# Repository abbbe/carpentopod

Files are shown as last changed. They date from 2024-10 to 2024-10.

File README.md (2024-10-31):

# Table of Contents

- [Credits](#credits)
- [Community](#community)
- [Downloadable Content](#downloadable-content)
- [Intro](#intro)
- [Design](#design)
  - Linkage
  - Legs
  - Leg Pair + Frame and Crank
  - Frame and Crank
  - Gearbox and Frame
  - Crank
  - Six Legs
  - Full Assembly
  - Editable Design Files
- [Printing](#printing)
- [Assembly](#assembly)
- [Electronics](#electronics)
- [Firmware](#firmware)

**Update 2024-10-31**

* The square shafts were originally printed in PLA-CF, but two out of 3 got damaged very quickly. I reassembled the whole thing using 8x8mm steel rods. Here in Belgium these rods can be bought in DIY stores. You'll have to cut them to size, see dimensions in the build log below.
* Manually chamfered the round parts of the cranks, to make it less likely to collide with the bottop part of the legs.
* Added a M8 nut which hides under the outter black spacers, to make the frame more rigid.
* Added rounded shoes (printed in PETG), to let feet slide sideways during turns.

All these changes (except chamfer of the cranks) is in the latest version of STEP models.

# Credits

This project was inspired by [Carpentopod](https://www.decarpentier.nl/carpentopod) created by Giliam de Carpentier, all credits should go to him.

# Useful Content

Here is a Youtube clip of the [thing walking steered using Nintendo controller](https://youtu.be/jmLX-odWrtY):
IMAGE ALT TEXT HERE (https://www.youtube.com/watch?v=jmLX-odWrtY)

The latest Fusion 360 models in STEP format is uploaded into the [STP/](https://github.com/abbbe/carpentopod-v43/tree/main/STP) folder on GitHub. Normally the STEP file includes all the subcomponents. (If you want individual models of the elements described in "Design" section, check previous commits). Once you open the model you should get something like this:
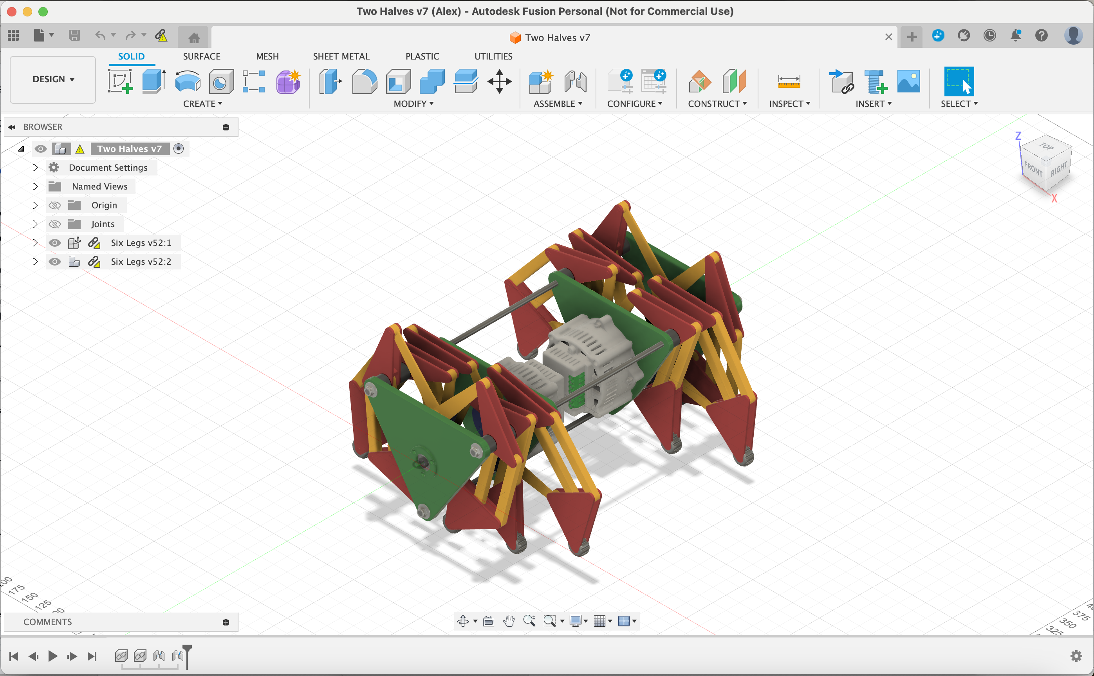
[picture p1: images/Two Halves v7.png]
Two Halves v7 - Thumbnail


An interactive 3D model is available on the [Autodesk site](https://a360.co/3A7hhCD).

Here is a screen recording of the [animation of the joint movements in Fusion 360](https://youtu.be/IclcQic5kn8) on YouTube. Done from different view angles, with some legs and plates removed to make the crankshaft movements visible. I did not recreate it since the original upload, so there are no shoes (you can see those via the Autodesk link above).

Printable 3MF files are uploaded into the [3MF/](https://github.com/abbbe/carpentopod-v43/tree/main/3MF) folder. Made in OrcaSlicer, printed on a Bambu X1C with 0.4mm hardened steel nozzle (see the Printing section below for more details).

The models are also published on [Printables](https://www.printables.com/model/1052837-carpentopod-v43).

I have created a [thread](https://discord.com/channels/1299814326185627702/1300201396834140271) on Giliam's Discord server, if you have any questions feel free to ask there. Or create GitHub issue or a pull request.

# Intro

I have been playing with Fusion 360 and various linkages for couple months when I saw a video of the [Carpentopod](https://www.decarpentier.nl/carpentopod) published by Giliam De Carpenter. He was kind enough to release exact linkage dimensions. I figured it could be a nice Fusion 350 challenge to design the mechanism behind the scene.

As you will see below, I have focused mostly on the mechanical side, not the artistic value of the piece. There is rudimentary electronics curcuitry and firmware to control it, I have described it on the high level at the end of the document.

At this point as I have no particular plans to continue with this project. If you found this design entertaining or useful, I will be happy to hear about it. Feel free to contact me if you have any questions.

And as far as any intellectual property (accidentally) created by me goes -- I am licensing it away under two conditions: (1) you put a star to this Github repo and (2) you will not use it for any military purposes. **Make robots, not war!**

# Design

## Linkage

I have turned the original linkage diagram black and white for easier printing and named each joint.
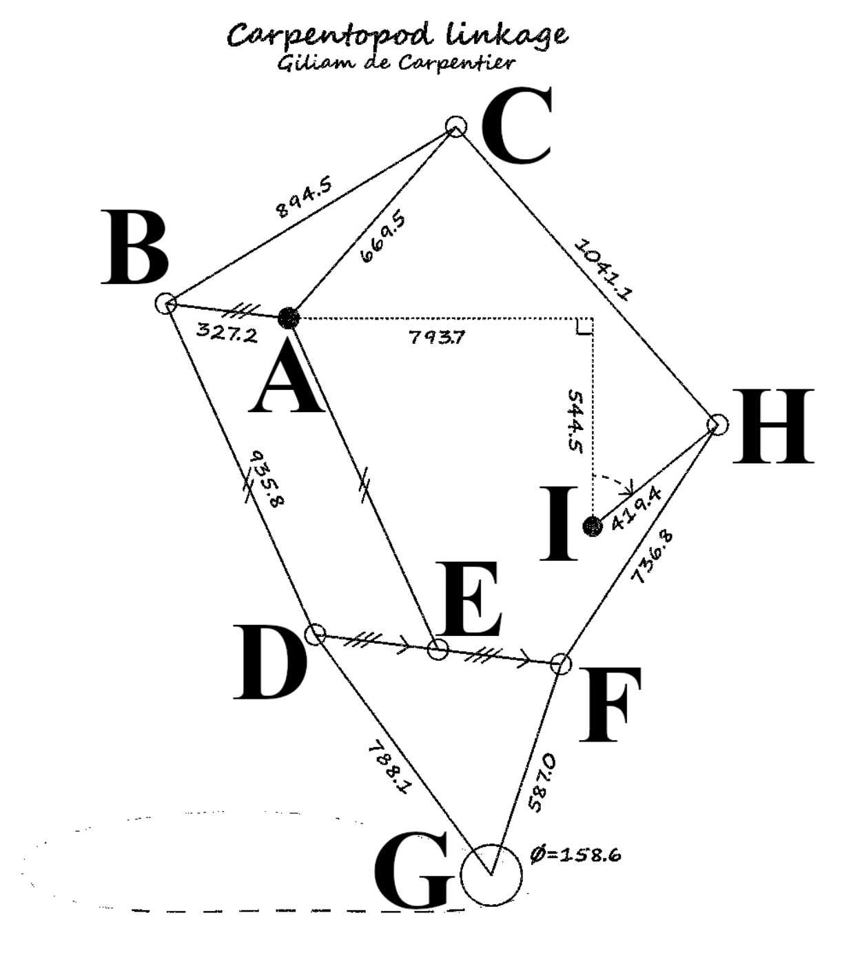
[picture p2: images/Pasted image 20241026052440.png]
Linkage Diagram


## Legs

The first part I designed was a leg. I have made an attempt to parameterise the design. It was not obvious what units Giliam's diagram used exactly, so I have included a scaling factor which I can tune the size of the model for my printer.
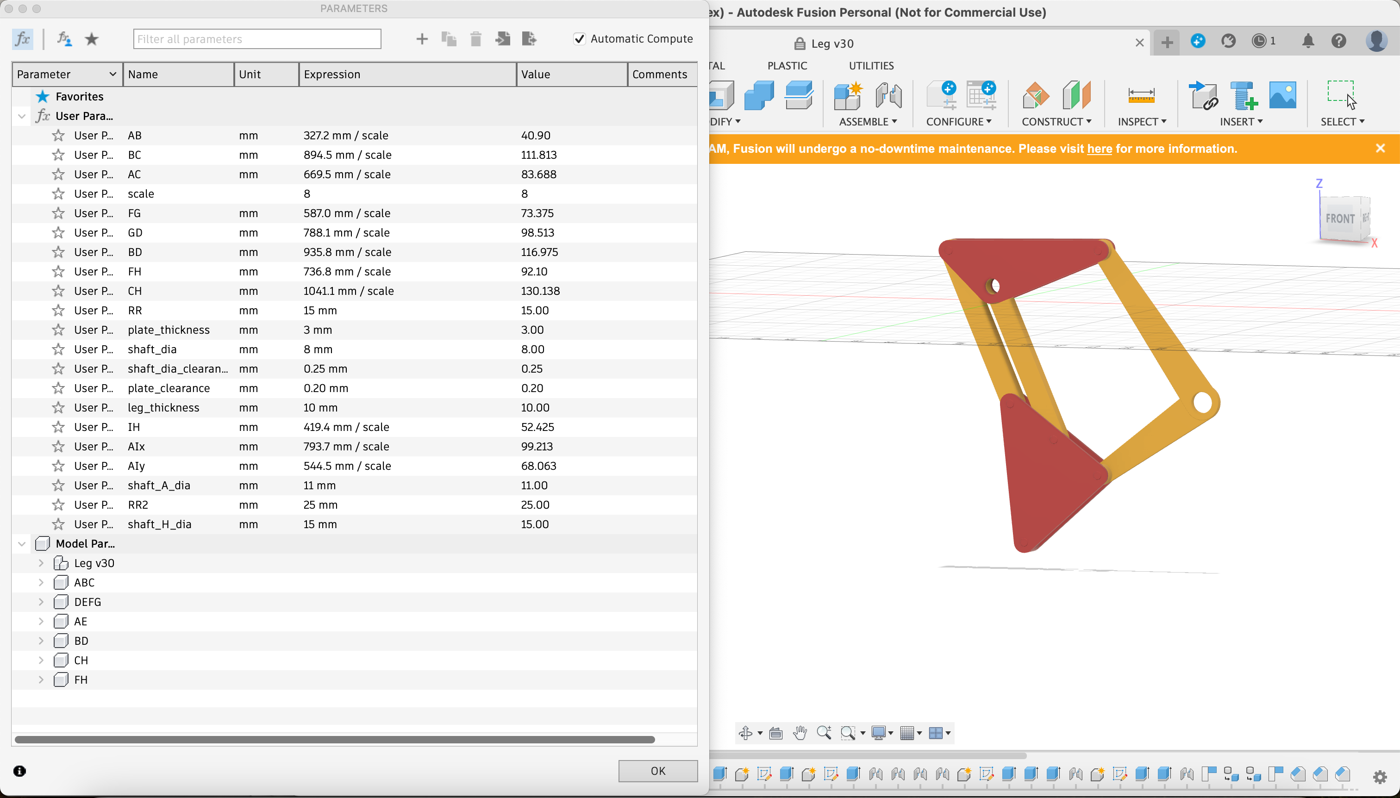
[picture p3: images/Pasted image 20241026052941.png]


Unfortunately, I couldn't find a way to share parameters between designs in Fusion 360. So some of these values ended up being copy-pasted into other designs. If you know how to do this properly, please tell me.

The design is as simplistic as it gets, I have made no attempt to replicate the beautiful curves of Carpentopod's legs. Here is another view without the top plates:
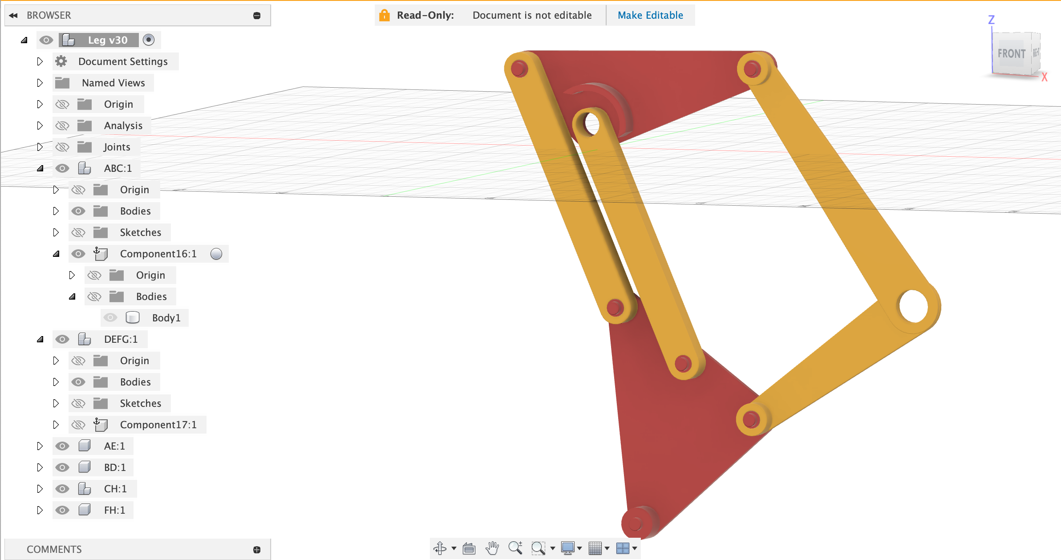
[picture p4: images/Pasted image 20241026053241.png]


To keep things 3D-printable I had to make a separate spacer:
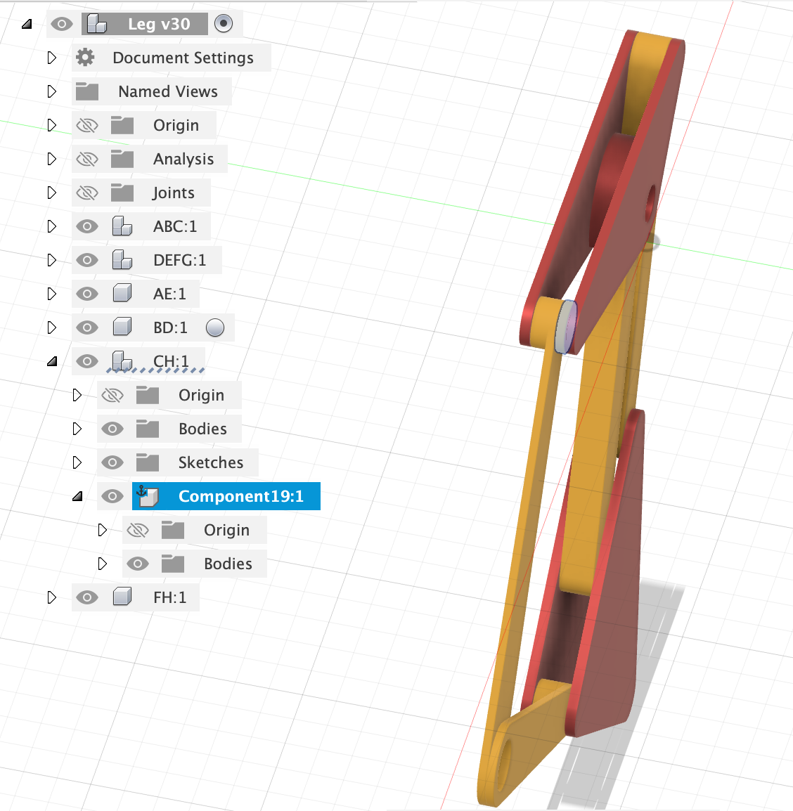
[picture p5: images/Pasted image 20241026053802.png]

I have randomly chosen the thickness of the larger levers (AE, BD) to be 10mm. It means levers CH and FH became 2.5mm thick (there was no spacing in between the levers, but there is spacing between the yellow levers and the red plates). This turned out to be a bad choice, because when I 3D-printed it using normal 0.20 layer height, the slicer makes it slightly bigger, something like 2.60. Not a big deal as such, but 4 levers stacked together (combined with other artefacts of 3D printing process) became too thick. I worked around this issue by printing using 0.16mm layer height.

## Leg Pair + Frame and Crank

Next I have put together a pair of legs.
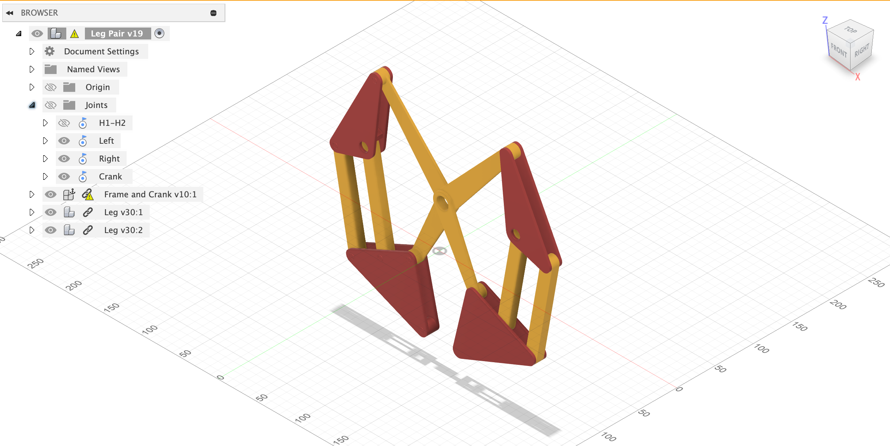
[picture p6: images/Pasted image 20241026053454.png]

H1-H1 joint is connecting H joints of the legs. Other joints you see on the picture is my way to help stacking the leg pairs later down the road. There is another design included into this file called Frame and Crank. Left, Right and Crank joints link the pair of legs to corresponding sketch points of that design.

## Frame and Crank

I have made a separate design file in attempt to work around lack of shared parameters in Fusion. It includes two sketches and no bodies.

Left, right and bottom circle on Frame sketch are the horizontal M8 rods which link the whole thing together. I have actually had another rod on the top, but eventually dropped it. The central circle is the motor shaft (point I).
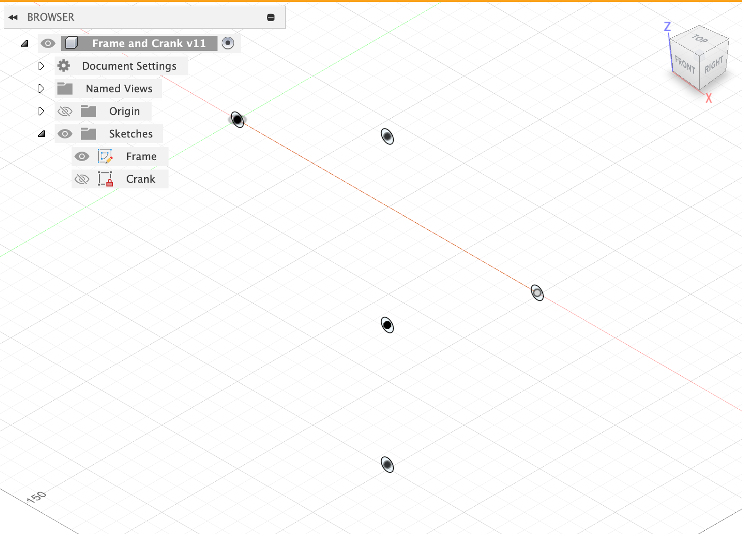
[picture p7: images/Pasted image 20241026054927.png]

The Crank sketch contains a circle positioned in the same place as the central circle (I) on the frame. Another circle is point H, which turns around point I.
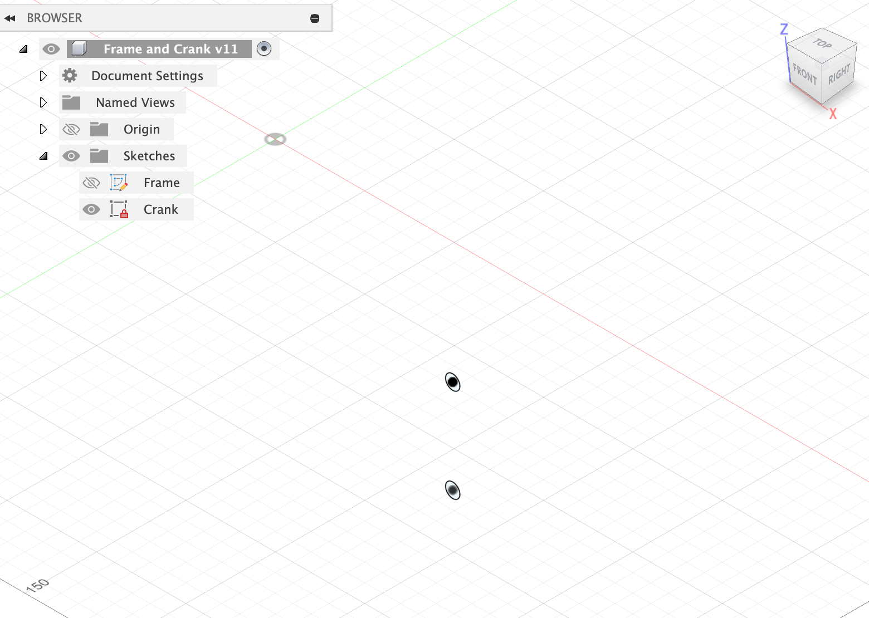
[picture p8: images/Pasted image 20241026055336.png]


This Frame and Crank design file is included into other design files. Unfortunately at some point I have edited this design without properly updating other design files. If I do it now, things fall apart. I am not sure how this problem can be resolved.

## Gearbox and Frame

The next design file includes the motor and a large plate to fix it on. I have used [OpenQDD v1 actuators](https://www.aaedmusa.com/projects/openqdd) designed by Aaed Musa (slightly adapted to use MKS ODrive Mini). These mighty things are probably overkill for this project, but I have just built a pair and had no better use for it yet.

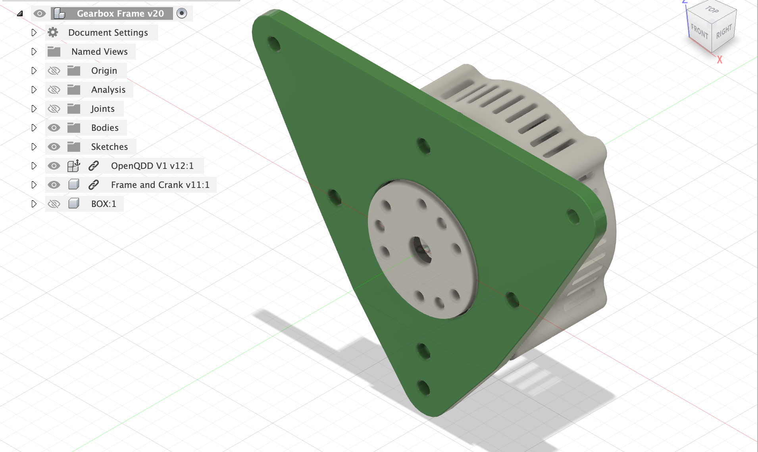
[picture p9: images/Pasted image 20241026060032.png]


## Crank

And here comes probably the most complicated part of my design, the crankshaft. I have spent probably a week trying to figure it out, then printed something rather ugly that survived for just long enough to allow me to come up with a rather nice design I think. It  consists of just 3 unique elements.

Two **RadialCrankShaft**. One will be combined with the motor output in the next design. Another is meant to be glued with a little lever which plugs into a ball bearing on the outer plate.
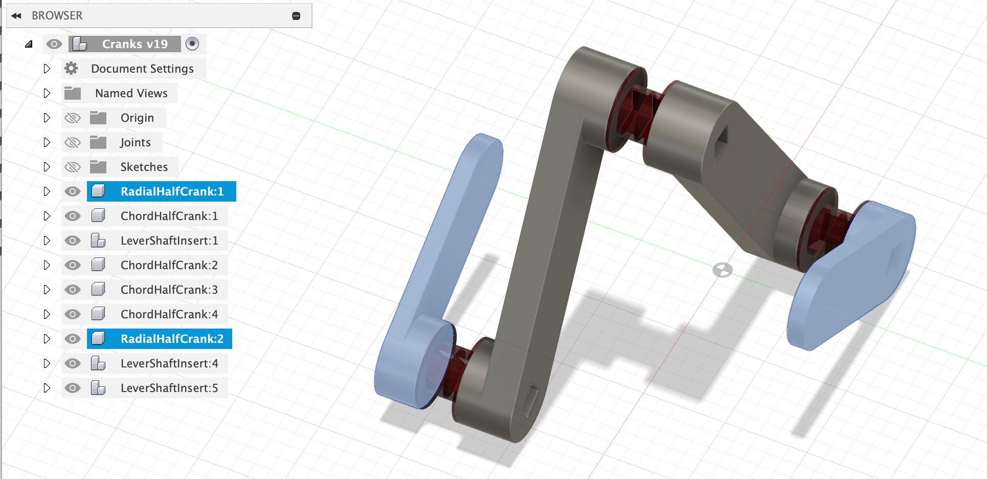
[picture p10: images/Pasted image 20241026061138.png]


Four **ChordHalfCrank** pieces, which are glued together back to back to make two components.
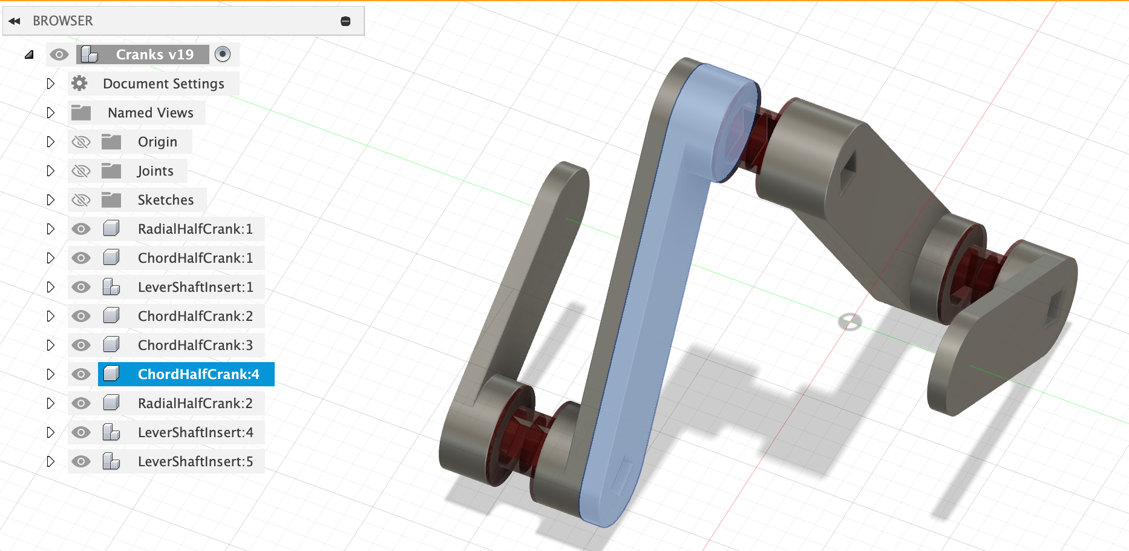
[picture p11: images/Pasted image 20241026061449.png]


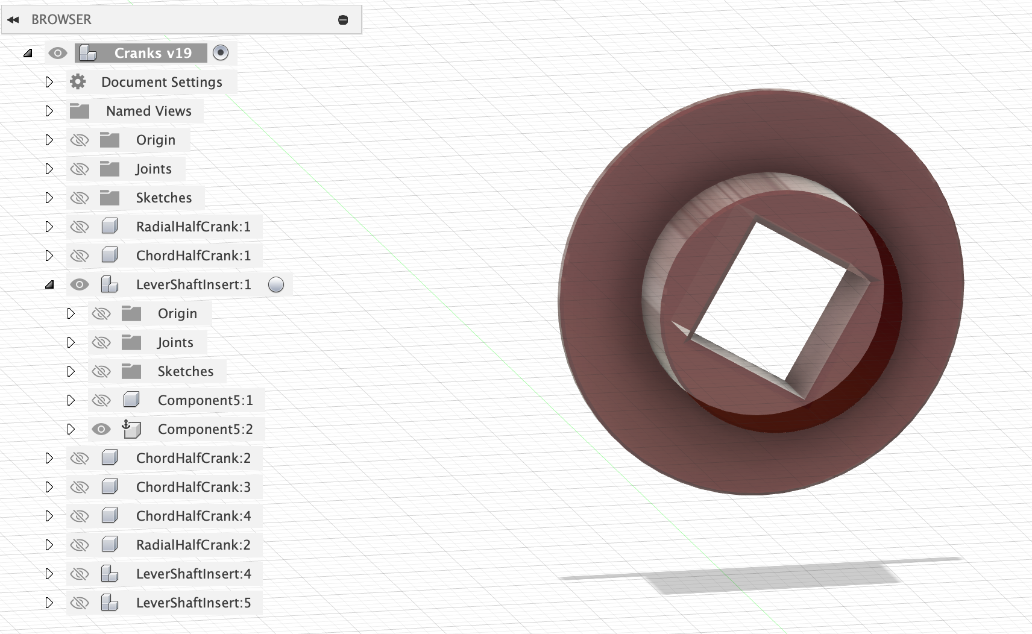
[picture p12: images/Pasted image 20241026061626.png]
Six inserts. 

I was not sure if the plastic will be strong enough, so I have chosen 8mm square shafts. I figured I can just use metal rods from any DIY store if 3D printed parts do not hold.

Originally the shaft were in this design too, but the length of the two of the shafts actually depends on other elements, so I have moved them to the next file.

## Six Legs

Finally, all of the above are assembled together:
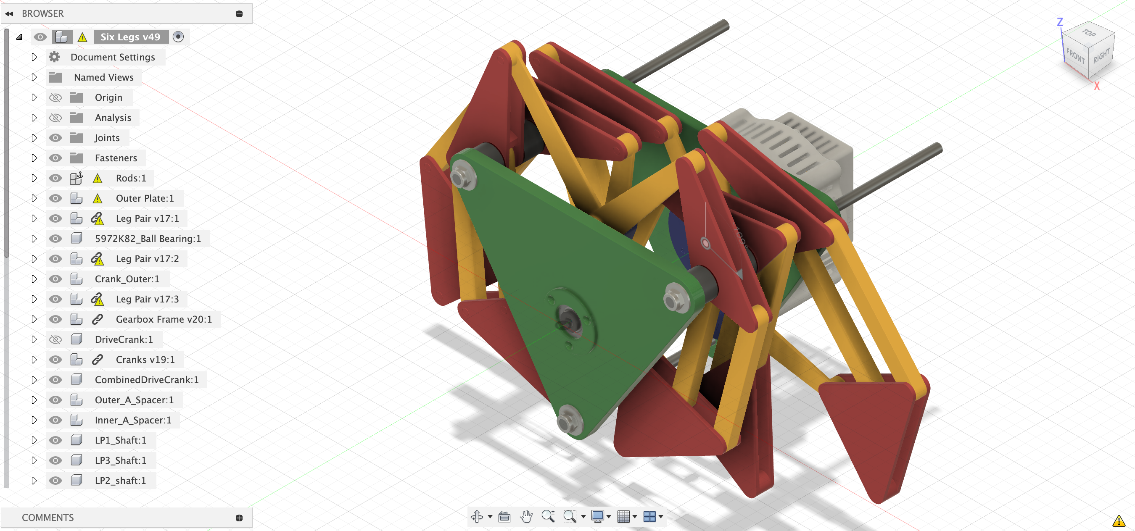
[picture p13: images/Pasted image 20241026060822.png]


I used M8 rods with nuts and washers to keep the whole thing together. They are 250mm long in this design, but in the physical world they are 500mm. Not all fasteners are included into Fusion 360 project, see the pictures/videos of the assembled contraption for finer details.

There is another dumb green plate. I was thinking about redoing them in black with a honeycomb pattern but this never happened. It embeds a ball bearing. I had a pair of 6001Z left from OpenQDD assembly, so I used them. Simple 608 would do the trick as well I am quite sure.

You can also see a bunch of black PLA spacers. There are also some inserts, rendered transparent red acrylic, but actually printed in grey PETG.

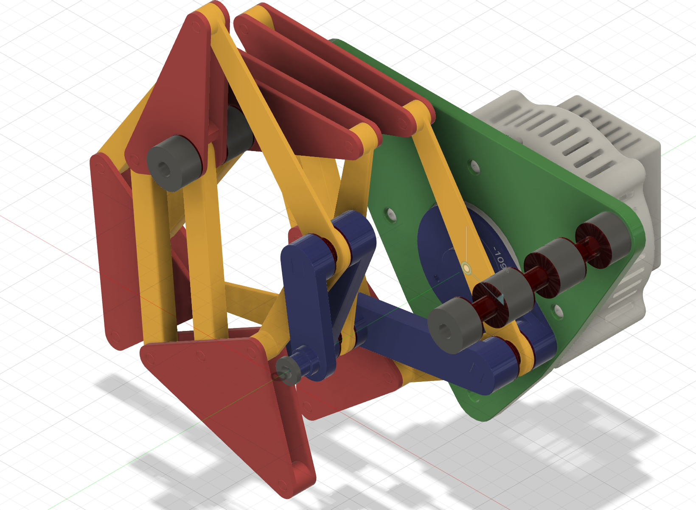
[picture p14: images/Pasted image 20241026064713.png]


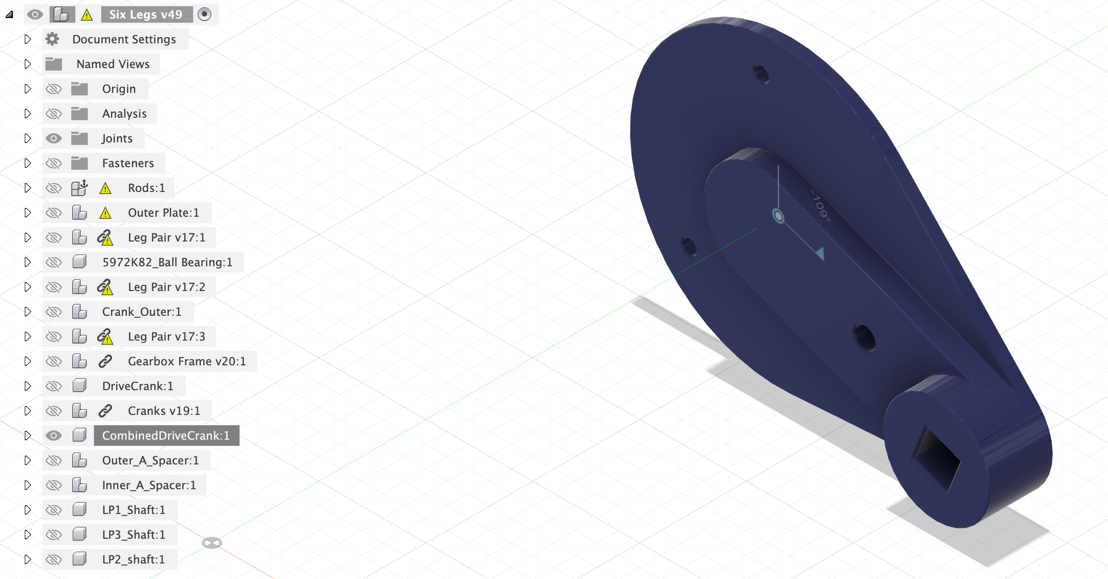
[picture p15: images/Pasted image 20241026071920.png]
The piece which gets attached to the motor is called CombinedDriveCrank. It is a combination of RadialCrank (from previous design) and DriveCrank component. If you regenerate 3MF files note that you only need to export the combined part. 
**Note the hole on the elevated part of this element is larger than two other M3 holes. It was mean to accommodate a head of M3 screw. It has turned out to be too small for my screw. Consider resizing it to 6mm or something.**

## Full Assembly

And here are just two halves joined together.
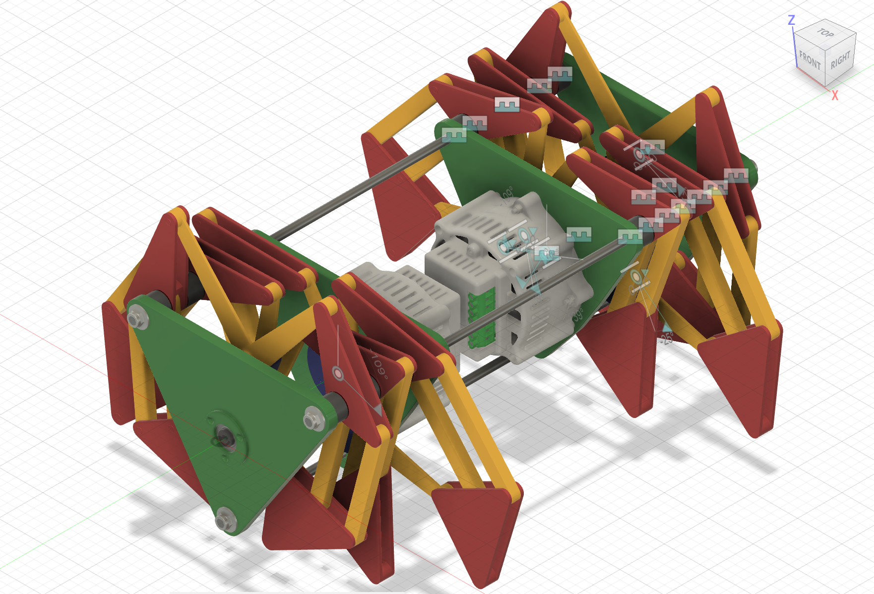
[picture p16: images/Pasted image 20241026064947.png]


## Editable Design Files

All the design files are published in in STP/ folder:
```
Leg v30.step
Leg Pair v19.step
Frame and Crank v11.step
Gearbox Frame v20.step
Cranks v19.step
Six Legs v49.step
Two Halves v4.step
M8 Cylinder v1.step
```

# Printing

See in 3MF/ folder:
```
Levers PLA YELLOW.3mf
Leg Plates PLA RED.3mf
Gearbox Frame PLA GREEN.3mf
Crank PURPLE PLA-CF.3mf
Inserts PETG-HF GREY.3mf
Spacers PLA BLACK.3mf
Outer Plate PLA GREEN.3mf
M8 Cylinder v1.3mf
```
If you need parts for both halves, you have to print all all these 3MF files twice (except the M8 cylinder tool).

STP files for OpenQDD v1 are published on [Aaed Musa website](https://www.aaedmusa.com/projects/openqdd). As I mentioned above, this is overkill by a large stretch, a simple DC motor with a gearbox should do just fine.

## Leg Levers

"Levers PLA YELLOW.3mf". I printed them in Bambu PLA Basic Red.

**If you print in 0.20mm it will not fit nicely (see explanations above).** 0.16mm layer height worked for me just fine. Settings in the 3MF file I publish are a blend of "0.16mm Optimal" and "0.20 Strength" profiles.

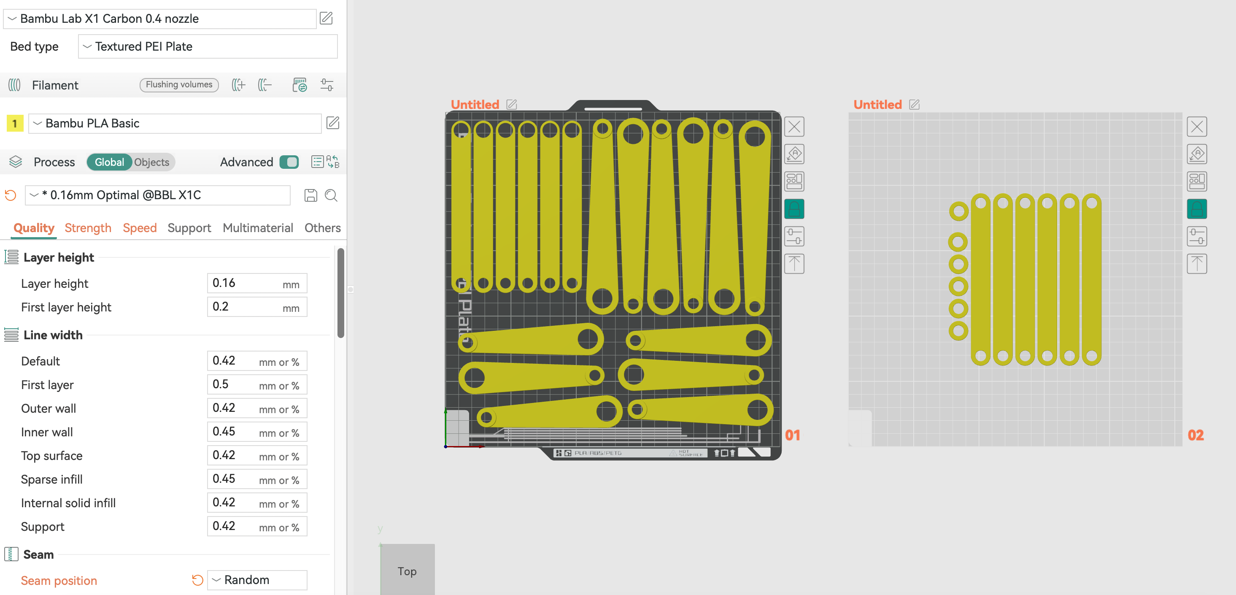
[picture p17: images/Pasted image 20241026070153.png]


## Leg Plates

"Leg Plates PLA RED.3mf" also gives you 3 pairs of legs. I printed it in Bambu PLA Basic Red using standard "0.20 Strength" profile with random seams.

Coulpe remarks:
* Plate 01 is packed rather tight. It prints just fine on my X1C, but you better remove [Shifty](https://makerworld.com/en/models/83480#profileId-89128)
* I am not sure if the orientation of parts on plate 03 is correct. If you care about the texture of the finished part - print one and see for yourself.
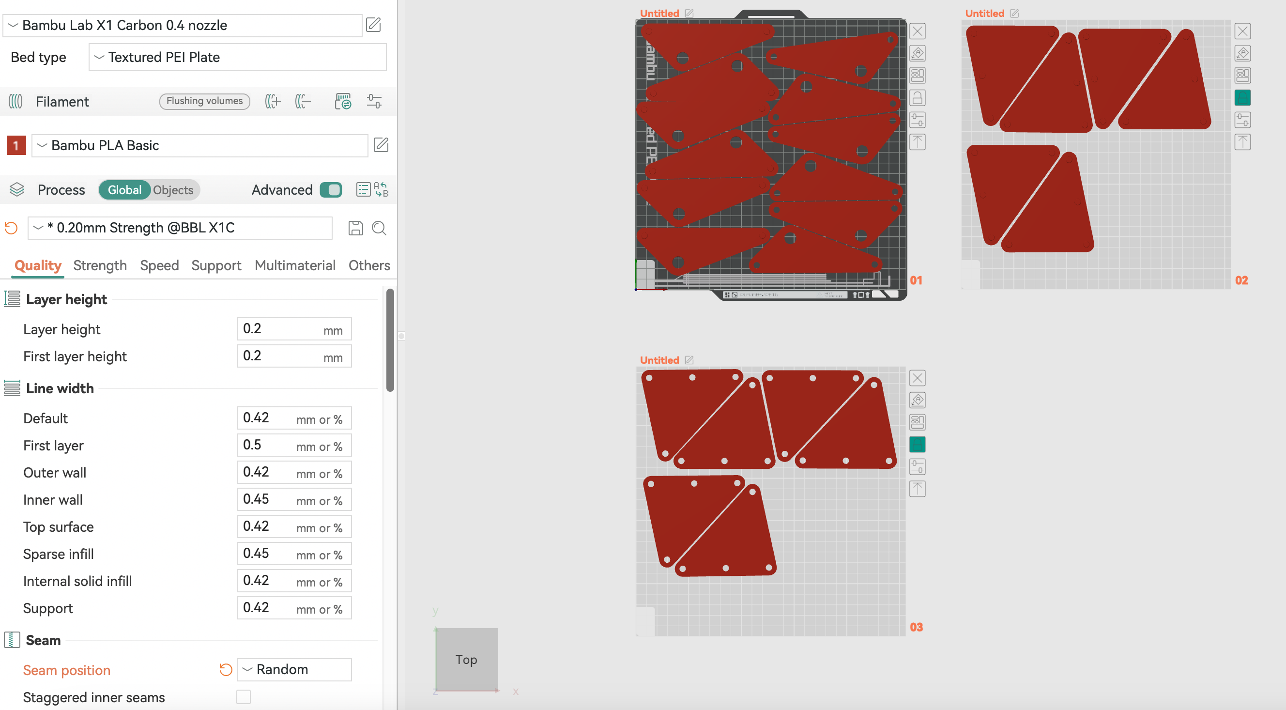
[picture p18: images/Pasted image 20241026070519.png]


## The crankshaft

"Crank PURPLE PLA-CF.3mf" was printed in purple Bambu PLA-CF, using the default "0.20 Strength" profile with random seams and 100% infill.
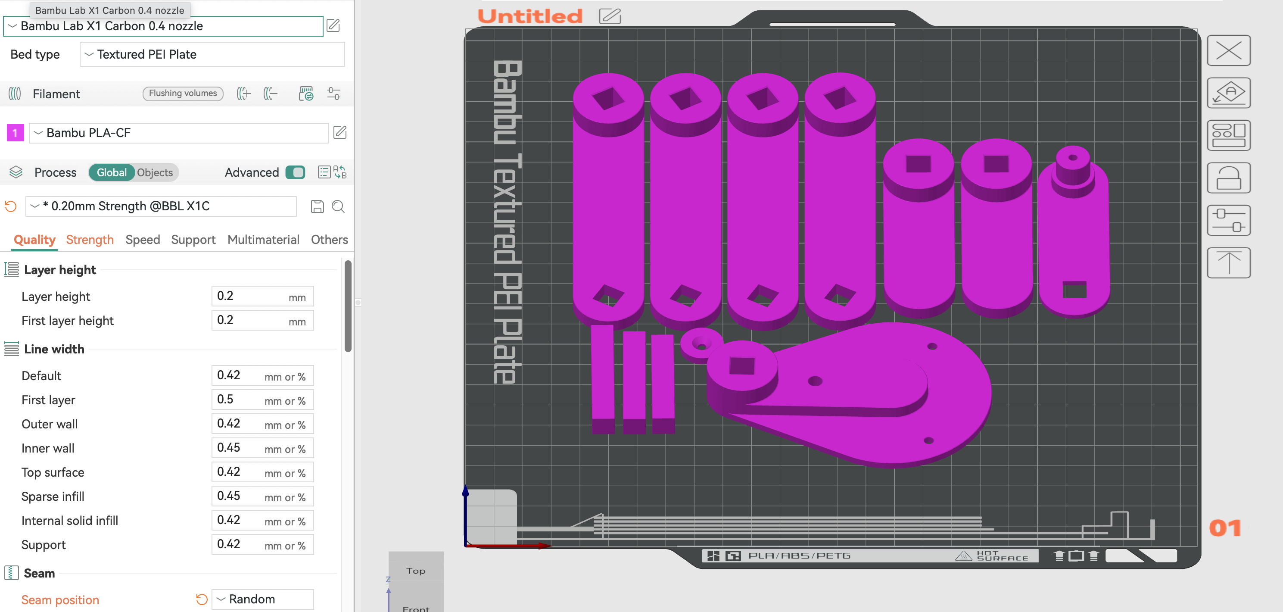
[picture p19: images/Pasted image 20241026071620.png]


## Spacers

"Spacers PLA BLACK.3mf" - probably the least critical element of the design. Printed in "0.20 Standard" process using black Bambu PLA Basic.
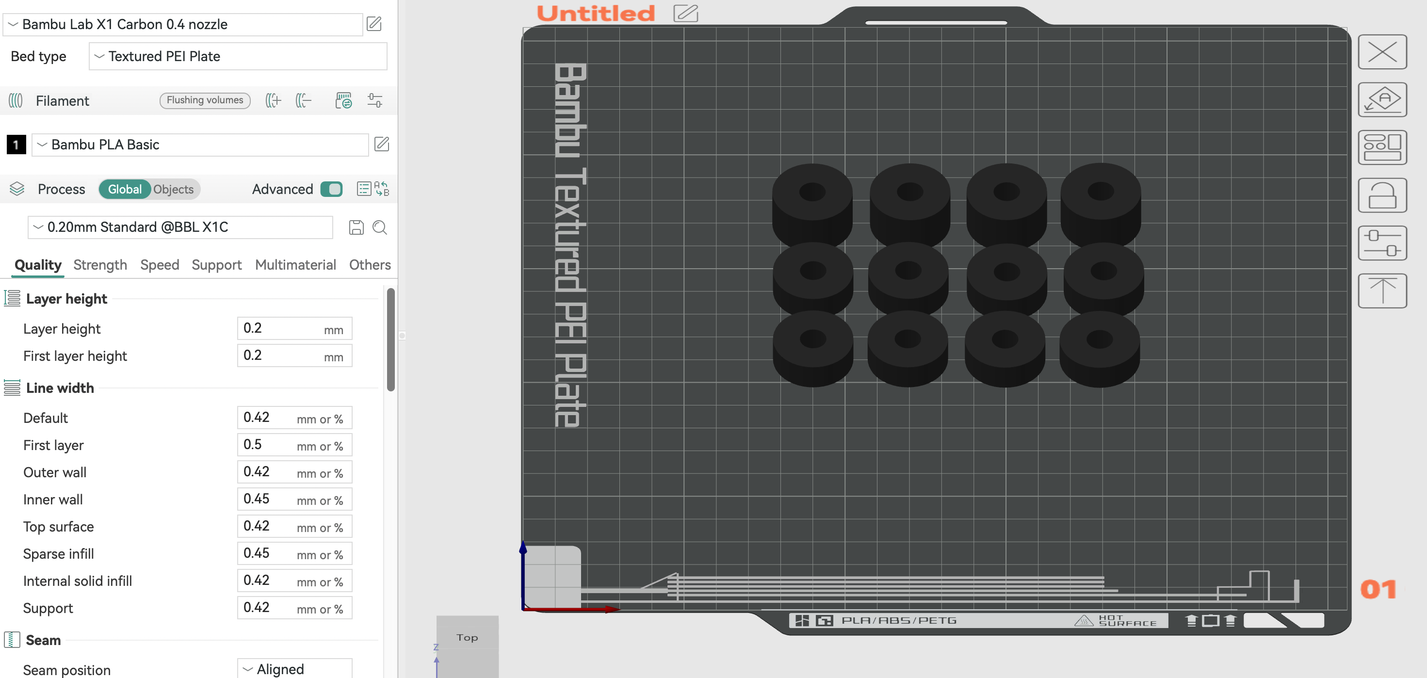
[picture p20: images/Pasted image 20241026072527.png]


When assembling you will be using two smaller spacers back to back in between the leg pairs. Next iteration of the design should probably have them merged to reduce the number of parts.

## Inserts

"Inserts PETG-HF GREY.3mf" - printed in Bambu PETG-HF using default "0.20 Strength" process with random seams.

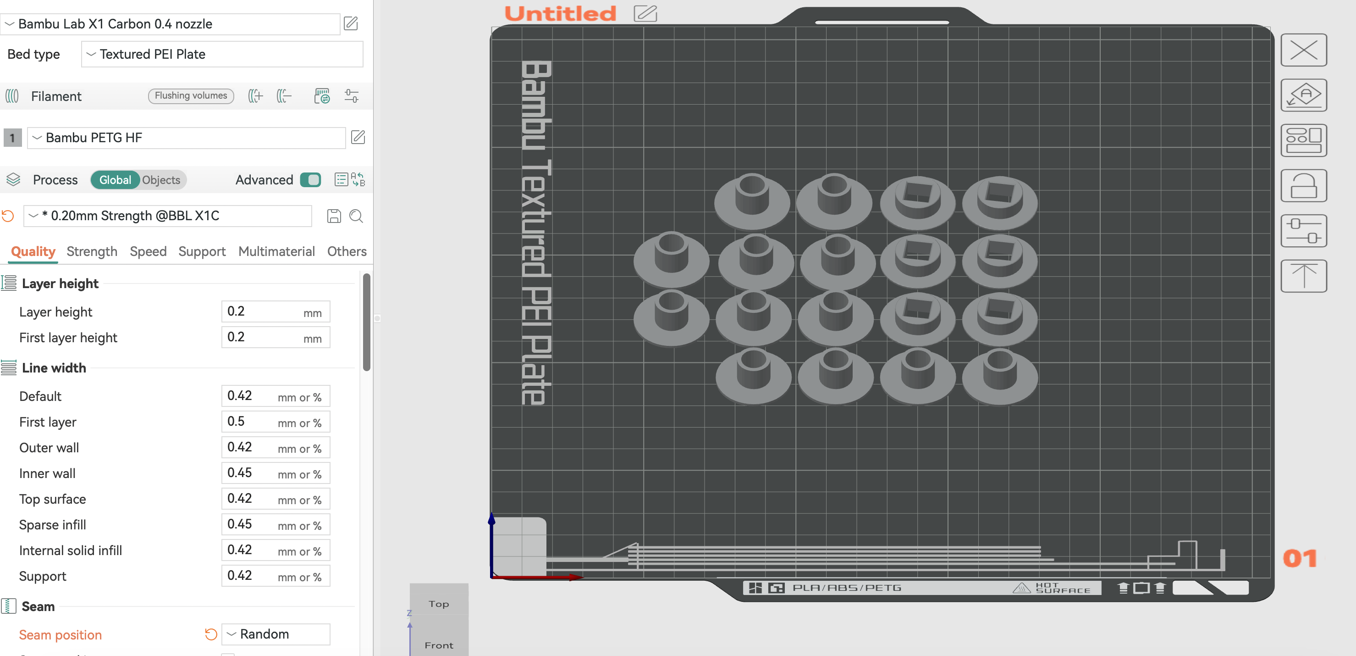
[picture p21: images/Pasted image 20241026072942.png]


## Green Plates

"Outer Plate PLA GREEN.3mf" and " Gearbox Frame PLA GREEN.3mf" are the elements I am the least proud of. Printed in green Bambu PLA Basic using default "0.20 Strength" process with random seams.
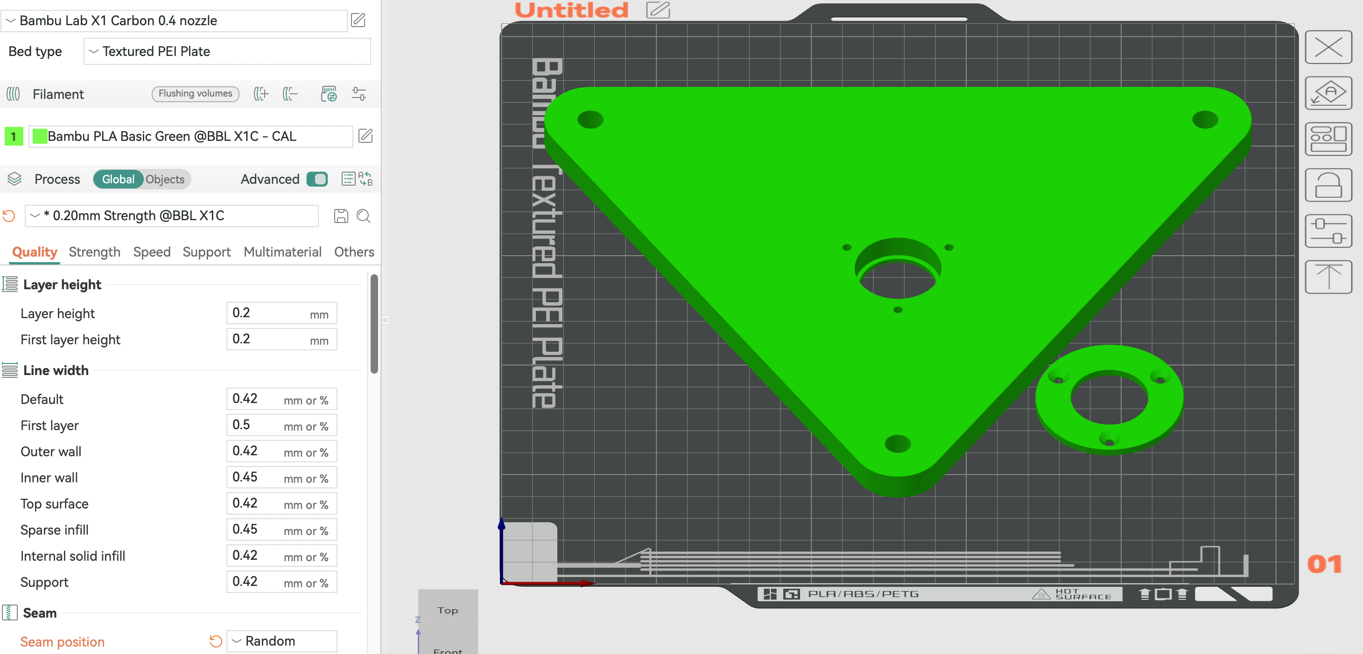
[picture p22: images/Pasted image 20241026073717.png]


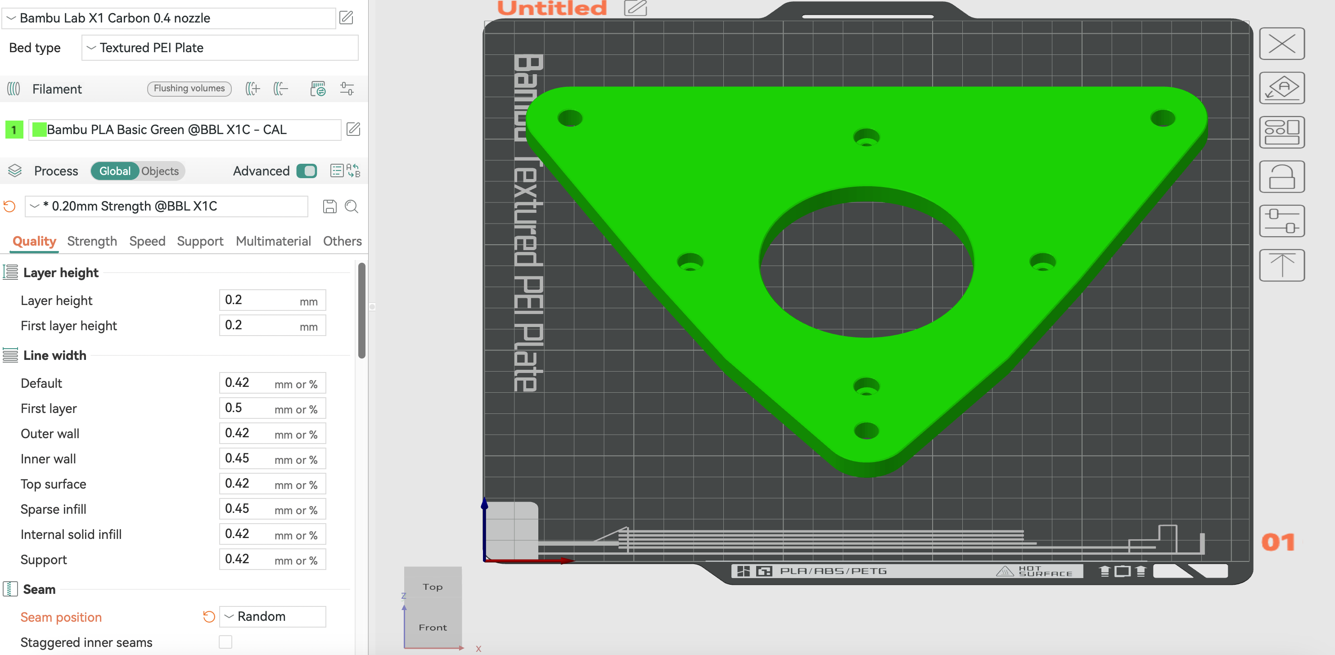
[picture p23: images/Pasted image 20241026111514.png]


# Assembly

The assembly process is rather straightforward. I have started documenting it towards the end of the project and only made photos of the assembly of one half. Please forgive the not so clean background.

### Preparation

Here we have a bunch of 3D printed parts:

Some weird optical illusion make the photo appear trapezoid, but it is a rectangle I swear ;).

They will go to into a half-assembled contraption.


Above you can see the motors are mounted on the frames and 3x 500mm M8 rods. On top of this I will use a handful of fasteners:
* 16x M8 regular nuts,
* 6x M8 nuts with plastic inserts,
* 9x large M8 washers,
* 4x small M4 washers,
* 3x M3x6 screws (to attach the output disk to the gearbox),
* 8x self-threading 3.5x12mm screws (to fix the ball bearing).

You will also need:
* a couple of 13mm wrenches,
* a screwdriver for your M3 screws,
* grease (I used [APP ST 250 PTFE Dry Lubricant Aerosol PTFE Grease](https://www.amazon.fr/dp/B004AHMVOM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)]),
* a deburring tool and 8mm drill bit.

You will want to debur the holes in the yellow levers to the point they rotate nicely. In my case something went wrong with the yellow PLA levers and I had to do a lot of deburring and even use 8mm drill bit to enlarge. _Next design should add chamfers to these parts._

You also want to sort the the purple square shafts by length:
* 41.40mm - goes into the motor crank disk at the very beginning,
* 43.40mm - used at the very end of the assembly,
* 46.40mm - the longest one, used in the middle.
_It would be nice to make some kind of identification marks on the shafts ot make them all same length_.

## Mount the Gearbox and Frame

Move a couple of M8 nuts and washers down the M8 rods. If you bothered to print the M8 cylinder you can move two nuts in one go.
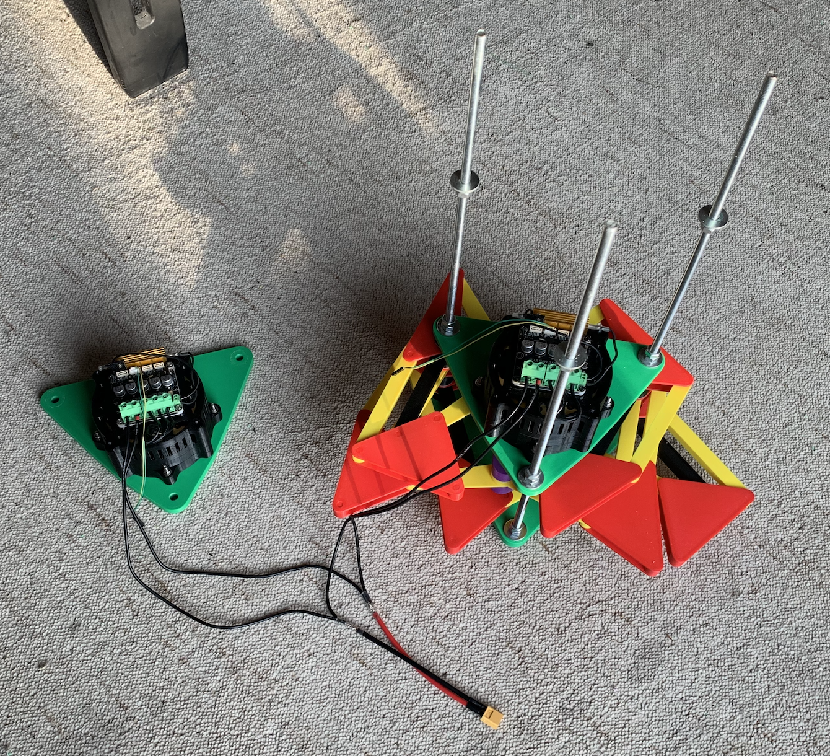
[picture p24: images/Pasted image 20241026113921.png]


Put the gearbox on top, add the spacers and a washer with a couple nuts on the bottom rod. Put the first shaft (the shortest 41.40mm one) before screwing in the purple part and mount it on top of the gearbox.
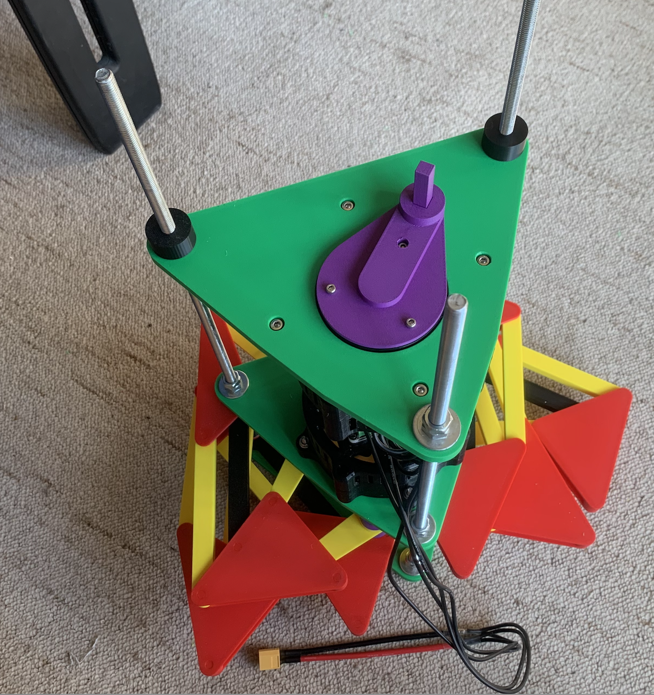
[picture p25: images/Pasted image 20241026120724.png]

As I mentioned above, the hole in the RadialCrank element turned out too small to fit the head of my M3 nuts. I used a 6mm drill to widen it. There will be no force tearing this plate off, but it is better not to drill it through (like I almost have done). _The next design iteration should fix this little bug._

## Legs

The next step is to assemble the legs. Use plenty of grease on all the axes and on the faces of the yellow levers around the large hole.
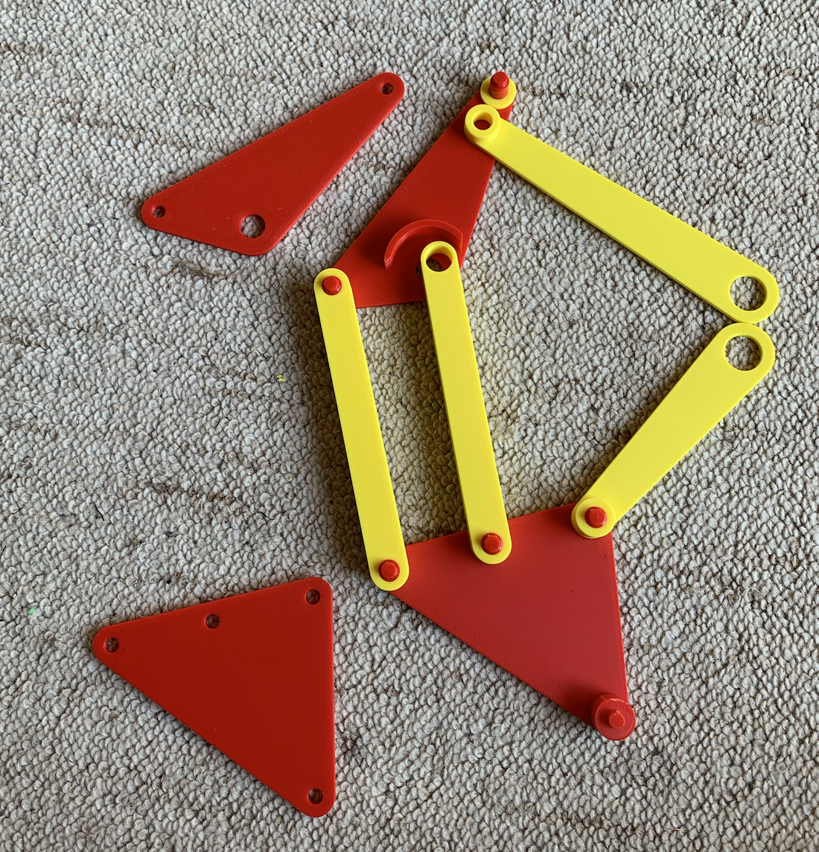
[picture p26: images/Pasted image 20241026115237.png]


The covers just nap into place.
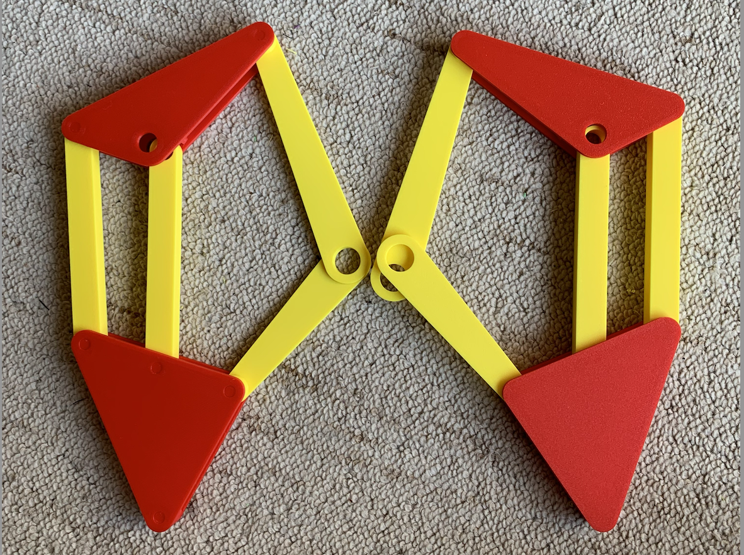
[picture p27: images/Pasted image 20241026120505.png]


Put the grey inserts, grease it all.


## Mount the First Leg Pair

Normally everything just slides into place. In my case the PETG inserts were probably over-extruded a bit, it took quite some force to push them down the square shaft, but it worked. _You better calibrate your PETG and PLA-CF extrusion and/or add tolerances_. Again, don't forget to grease the inserts.
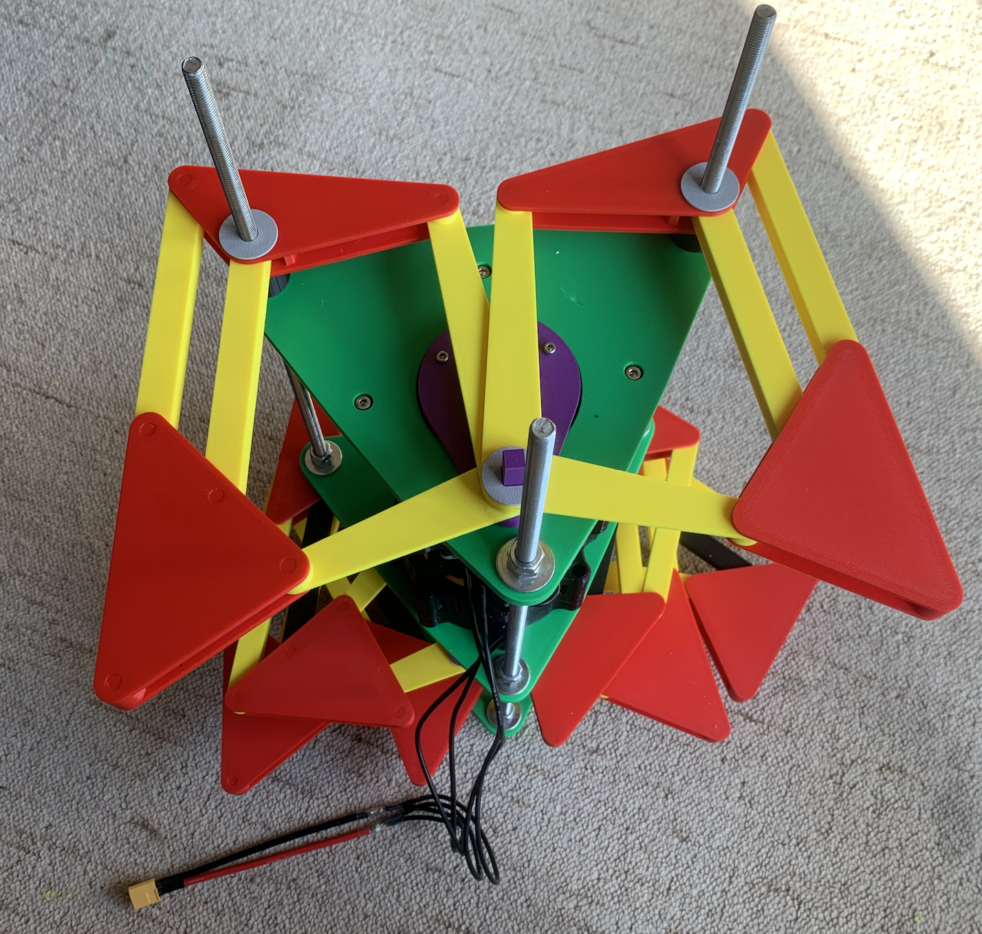
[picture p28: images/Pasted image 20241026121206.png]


## The crankshaft

Now it is time to glue the shaft together. I used some contact glue to fix the ChordCranks together. They are all identical, just make sure the square holes are aligned. _A better design would include some alignment pins I guess_.

Here is the final result:
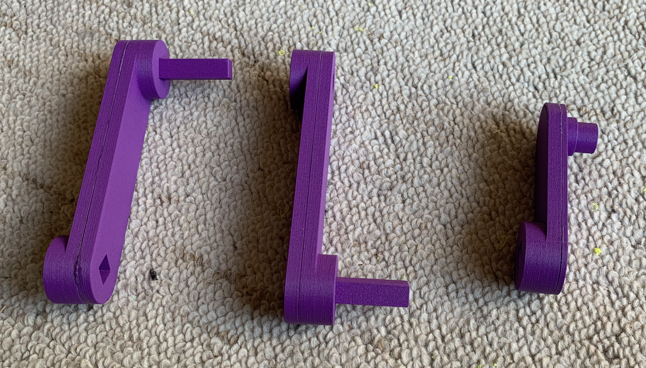
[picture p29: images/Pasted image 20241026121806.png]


On the photo below I have put all the elements of the crankshaft together just to give you an idea of how it looks like inside the mechanism. To continue the assembly process you obviously only need one element in place so **the photo below is for illustration purposes only and is not a real assembly step**.


## Assemble Two Remaining Leg Pairs

I guess it is straightforward to assemble and mount the remaining two pairs of legs.
* In between the leg pairs go the black PLA spacers. Two spacers go on each M8 rod one after another. _There is no good reason for it and an improved design should have these two spacers merged I guess._
* The second shaft is the longest one (46.40mm) and the last one is the shortest one (43.40mm).
* Note there are no stoppers and nothing stops the shaft from slipping away. It was not a problem for me in practice, the shafts fit just right and do not slip away. _A better design would include some stoppers and/or side screws to fix the shafts in place_.

Here is a photo of 2nd pair of legs mounted.


## The Last Step

Finally, you add:
* longer black spacers (one piece per M8 rod),
* the last crank shaft,
* another couple of M8 nuts and a washer on the bottom M8 rod.


I don't have photos of the assembly process of the green plates, because those were made at the very beginning of this project. Just snap the ball bearing in place and secure them with the ring and 3 screws.

Finally, mount the green plate on the M8 rods, push the outer end of the purple crankshaft into the ball bearing, and fix the purple washer with another screw.
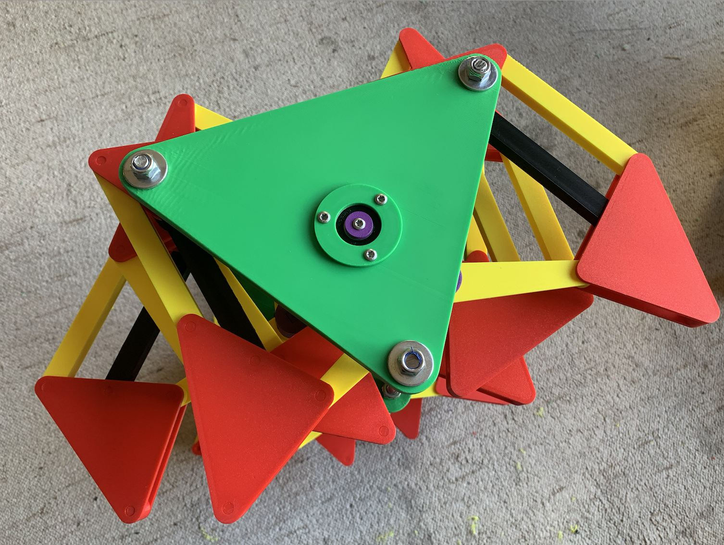
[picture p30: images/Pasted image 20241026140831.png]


## Fully Assembled View
Here's how it looks in the horizontal position:


With electronics (the serial links to the ODrives are not attached):


Fully assembled and switched on:
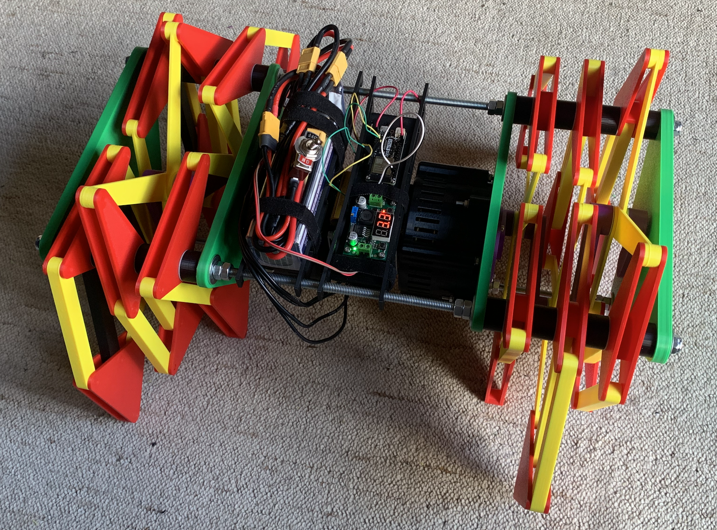
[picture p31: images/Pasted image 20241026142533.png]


# Electronics

I might document the electronic part later in greater details, but on the high level it consists of:
* A 22.2V LiPo battery with an XT60 connector
	* Aliexpress [HRB Lipo Battery 6S 5000mah](https://www.aliexpress.com/item/4000389770504.html?spm=a2g0o.order_list.order_list_main.71.22b418023OYCrn)
	* Might be overkill for this project
* A toggle switch
	* Aliexpress: [Large Current High Load Switch AMASS XT60](https://www.aliexpress.com/item/1005005224857810.html?spm=a2g0o.order_list.order_list_main.41.22b418023OYCrn)
	* Not sure I can recommend this particular model. The switch has failed to go OFF at least once
* Couple custom Y splitters to feed ODrives and the step-down converter
	* Aliexpress [Male Female Connector Plug with Silicon 12 AWG](https://www.aliexpress.com/item/1005003489220110.html?spm=a2g0o.order_list.order_list_main.53.22b418023OYCrn)
	* Next time I would probably go for a 14AWG, easier to work with
* A step-down converter
	* Amazon [Retoo LM2596 DC-DC Power Adapter Step-Down Module](https://www.amazon.fr/dp/B09QMDL7FH?ref=ppx_yo2ov_dt_b_fed_asin_title)
	* Seems to work fine, but very bulky
* LOLIN D32 board
	* Aliexpress [LOLIN D32 V1.0.0](https://www.aliexpress.com/item/1005005305131344.html?spm=a2g0o.order_list.order_list_main.124.22b418023OYCrn)
	* A very nice board in itself, but maybe not the ideal choice here. I bought it for something else because it has on-board LiPo battery charging circuits. This is quite pointless and even counterproductive as one has to add an extra wire to be able to power the board off external source.
* Custom serial cables, to control ODrives from LOLIN D32. Those are specific to OpenQDD, no point to got into any details here.

The LOLIN D32 / DC-DC converter / the batteries / the cabling -- all is screwed/velcroed to a  platform hanging in between the M8 rods.

# Firmware

The source code is published [here](https://gitlab.com/abbbe/bluepad-32-carpentopod-v-43/-/tree/carpentopod-v43?ref_type=heads), in the 'carpentopod-v43' branch of my fork of [Bluepad32](https://gitlab.com/ricardoquesada/esp-idf-arduino-bluepad32-template.git) repo.

To build the firmware [install the ESP-IDF 4.4 framework](https://docs.espressif.com/projects/esp-idf/en/v4.4/esp32/get-started/index.html) first (ESP-IDF command line tools worked for me on Windows 11). Then do the following to fetch my branch, build it, flash into ESP32, and run the serial console monitor:
```
git clone --recursive -b carpentopod-v43 https://gitlab.com/abbbe/bluepad-32-carpentopod-v-43.git
cd bluepad-32-carpentopod-v-43
idf.py build flash monitor
```

If things don't work use the hello_world project from ESP-IDF repo to troubleshoot your setup.

The following files were modified/added:

* main/sketch.cpp - existing file, calls couple functions defined in carpentopod.h from existing setup(), loop(), and processGamepad() functions.
* main/carpentopod.* - new file, manages ODrive's idle/running state, tranlsates joystick readings to velocity commands.
* main/odrive.* - new file, talks to ODrives over USARTs.

The firmware does the following:

* Initializes BLE controller and waits for a game controller to pair. This code comes from the upstream repo.
* Initializes ODrives and puts them in idle mode.
* If a controller is connected, it translates readings for Y axes of left and right joysticks to ODrive velocity commands. This is done by dividing the readings (-512 to +512 range) by 100, so ODrives go up to around 5 RPMs on full throttle.
* If a controller get disconnected, it switches ODrives to idle state.
* Monitors battery voltage and halts the system if voltage drops below safe value. _Ideally it should raise some alarms and put the system into deep sleep. Doable for ESP32, but ODrives do not support deep sleep._ 

Some remarks:
* The firmware contains tons of redundant code. Any game controller, a bluetooth mouse, a keyboard trying to join it will be accepted (but only game controller joystick events will be used).
* I could not figure out how to use Bluepad32 on my M1-based Macbook Pro - installation of ESP-IDF 4.4 fails there. Used Windows 11 instead.
* I used the [offline installer](https://objects.githubusercontent.com/github-production-release-asset-2e65be/342348458/8d0419b3-daf4-496a-97cf-b81cf14f8095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).
* PlatformIO did not work for me, my guess ESP-IDF 4.4 is too old, but I am not sure. VSCode with the ESP-IDF plugin works just fine, but you don't really need VSCode if you don't plan to edit code, command line tools which come with ESP-IDF 4.4 are enough.

THE END.

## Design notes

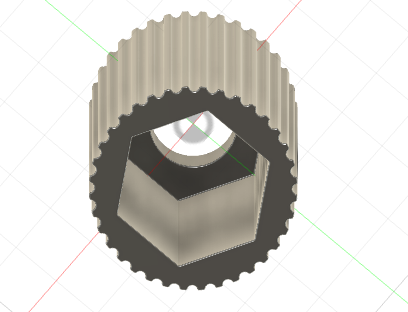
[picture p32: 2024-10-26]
images/Pasted image 20241026114257.png

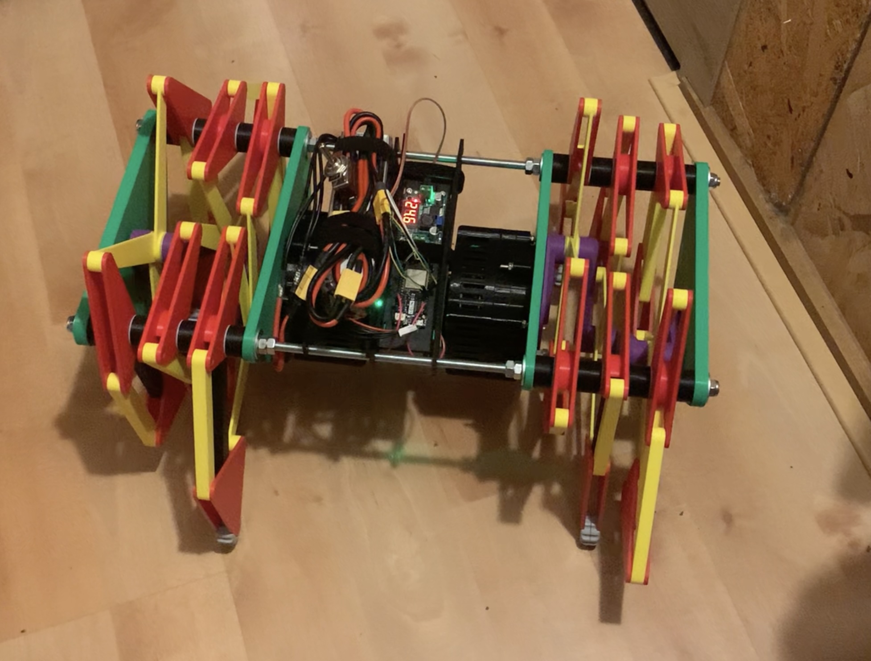
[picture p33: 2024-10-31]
images/Nintendo Walk.jpg

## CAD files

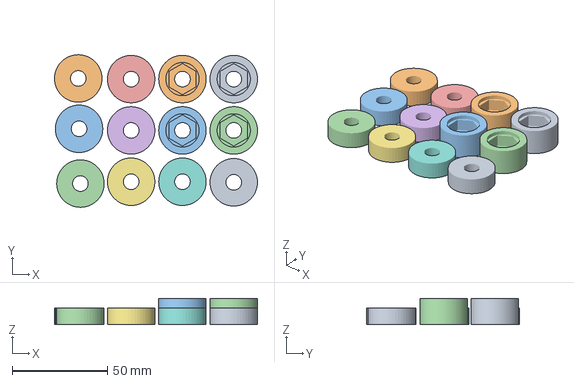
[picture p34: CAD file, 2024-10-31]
3MF/Spacers PLA BLACK.3mf
106.8 x 80.3 x 13.8 mm
OuterSpacerM8.stl x 4

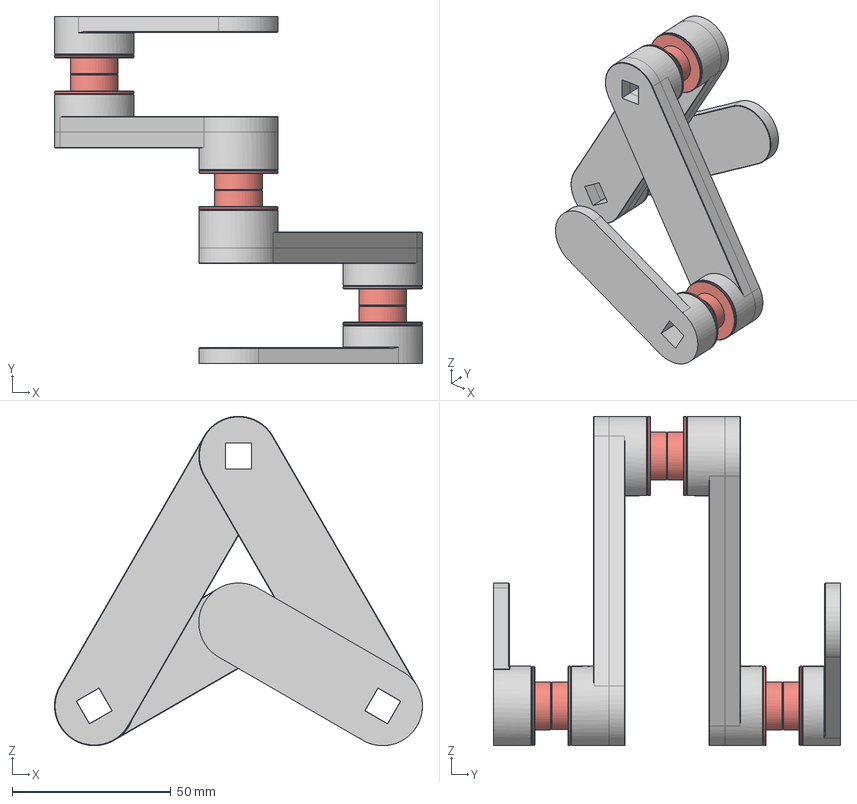
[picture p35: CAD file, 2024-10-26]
STP/Cranks v19.step
115.8 x 109.2 x 103.6 mm
RadialHalfCrank x 2
ChordHalfCrank x 4

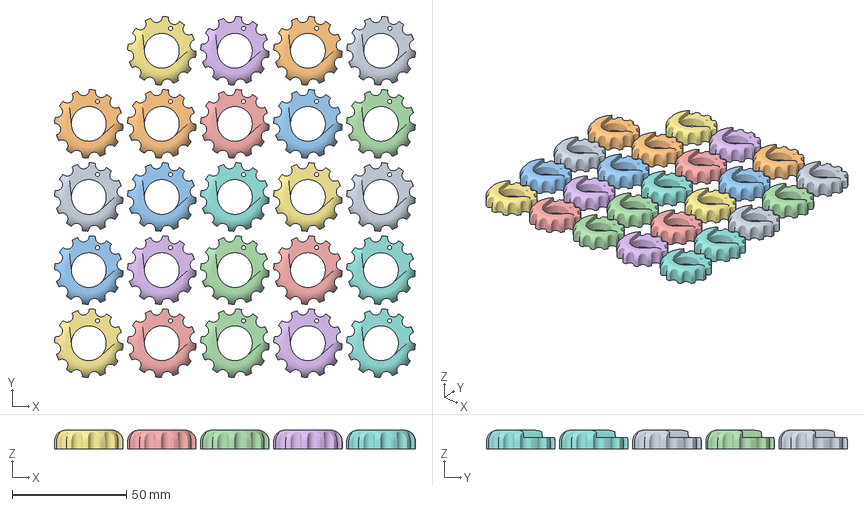
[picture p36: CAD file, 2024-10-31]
3MF/Feet v34.3mf
157.7 x 157.8 x 8.20 mm

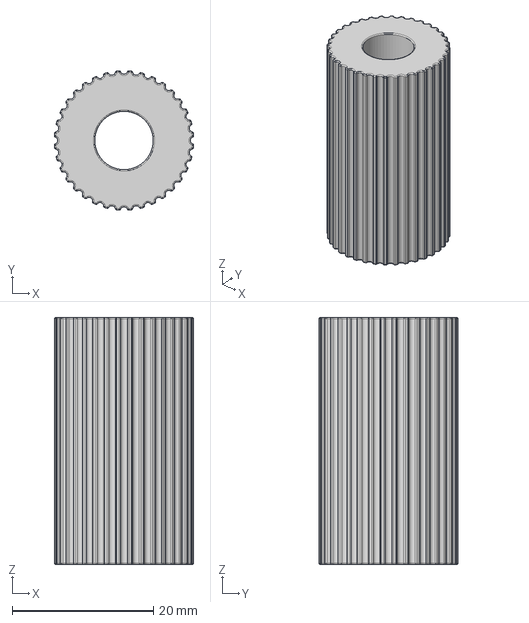
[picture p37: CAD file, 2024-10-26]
STP/M8 Cylinder v1.step
19.8 x 19.8 x 35.0 mm

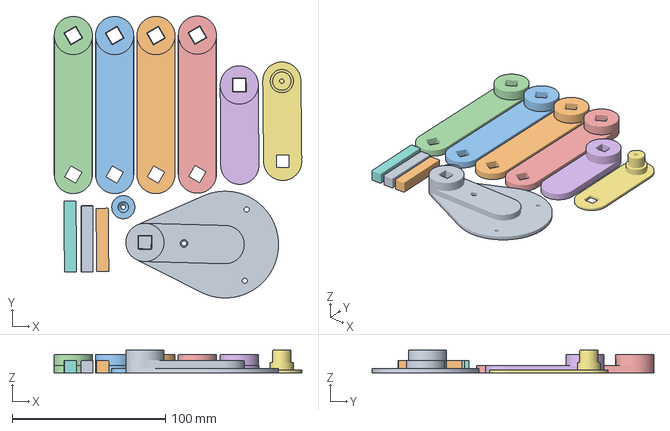
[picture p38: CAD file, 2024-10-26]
3MF/Crank PURPLE PLA-CF.3mf
161.8 x 184.2 x 15.0 mm

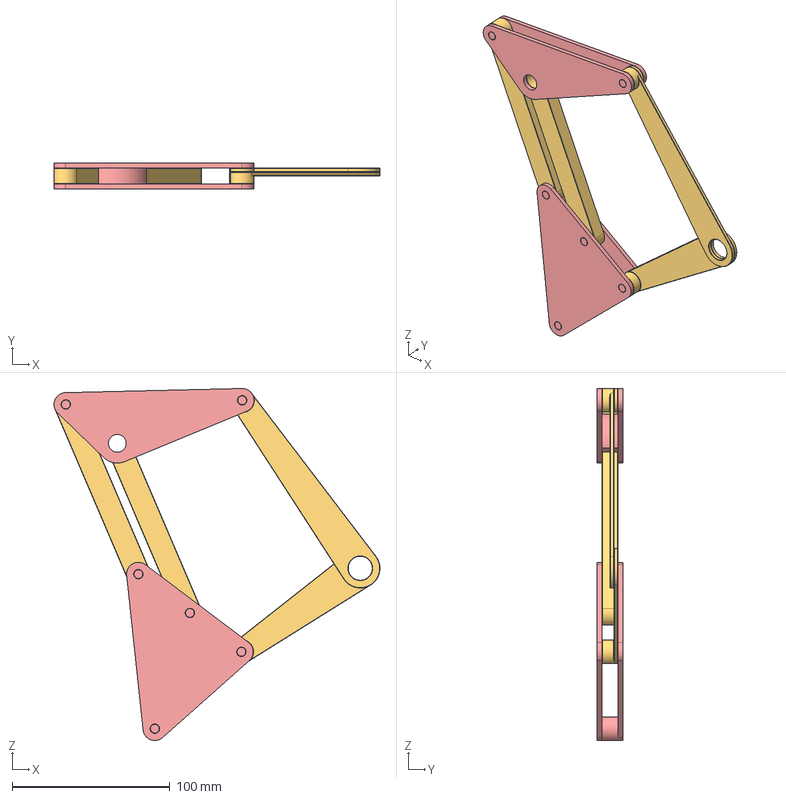
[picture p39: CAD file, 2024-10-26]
STP/Leg v30.step
206.6 x 16.4 x 223.1 mm
AE
BD
FH

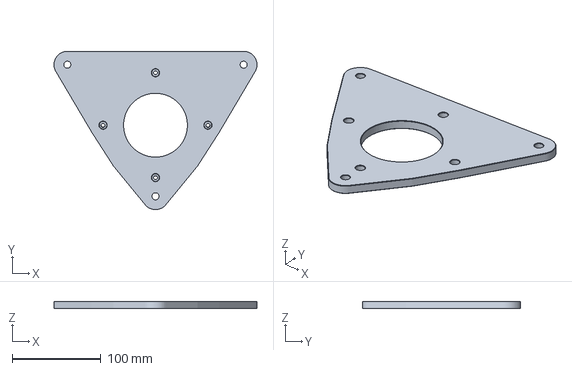
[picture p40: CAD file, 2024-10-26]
3MF/Gearbox Frame PLA GREEN.3mf
228.4 x 178.0 x 8.00 mm

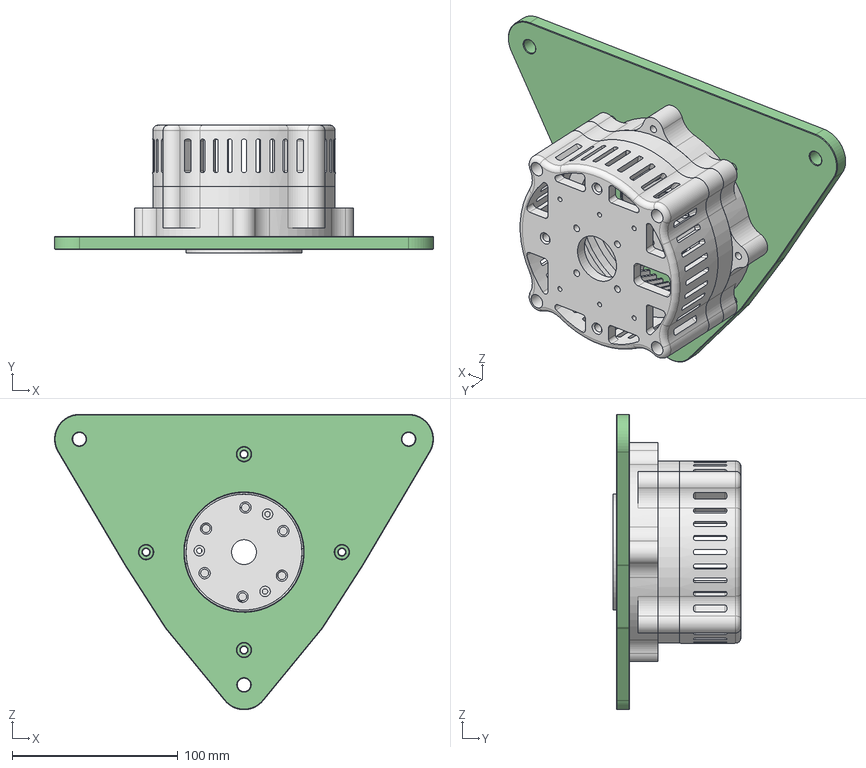
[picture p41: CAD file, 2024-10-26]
STP/Gearbox Frame v20.step
228.4 x 77.0 x 178.0 mm
BLDC_Casing
Captive_Bearing_Casing
Planet_Carrier_Bottom_1
gear_1
Frame and Crank

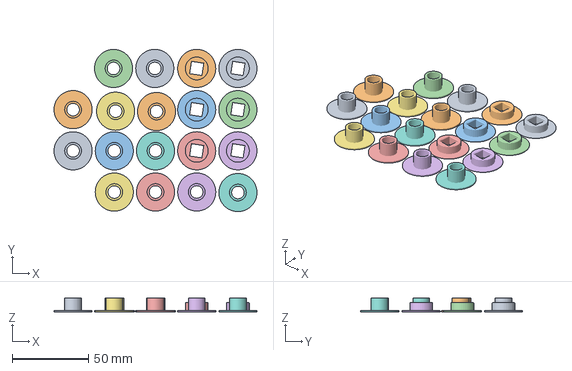
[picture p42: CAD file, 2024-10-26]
3MF/Inserts PETG-HF GREY.3mf
133.0 x 106.3 x 9.40 mm

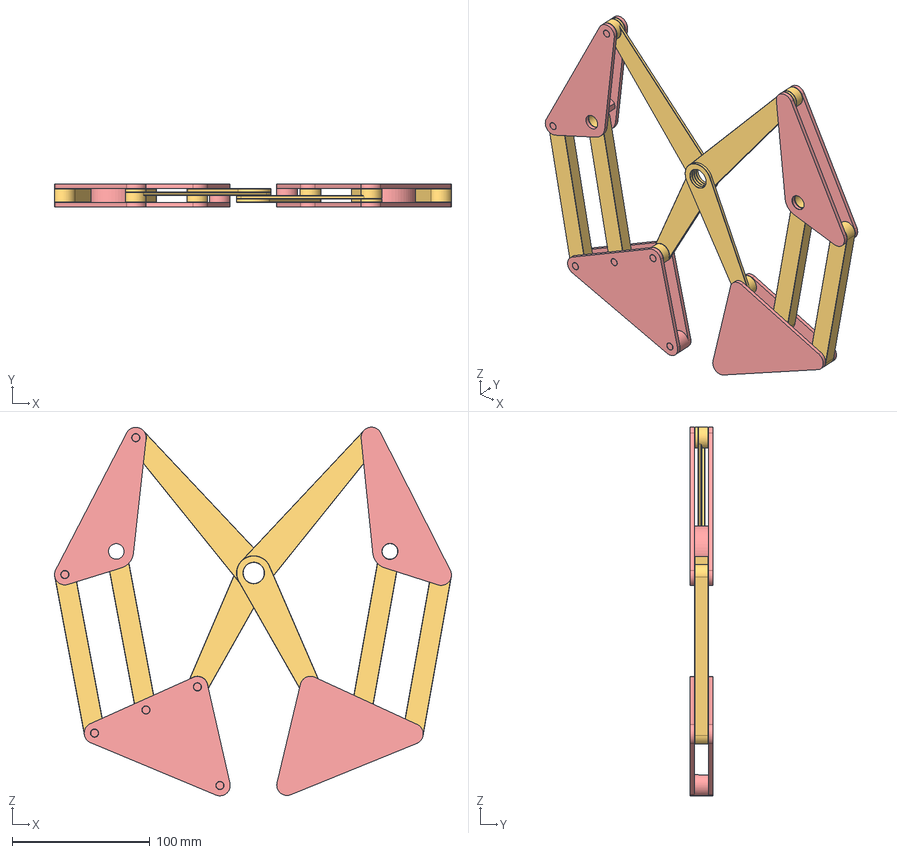
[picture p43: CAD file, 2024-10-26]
STP/Leg Pair v19.step
287.9 x 16.4 x 267.3 mm
Frame and Crank
AE x 2
BD x 2
FH x 2

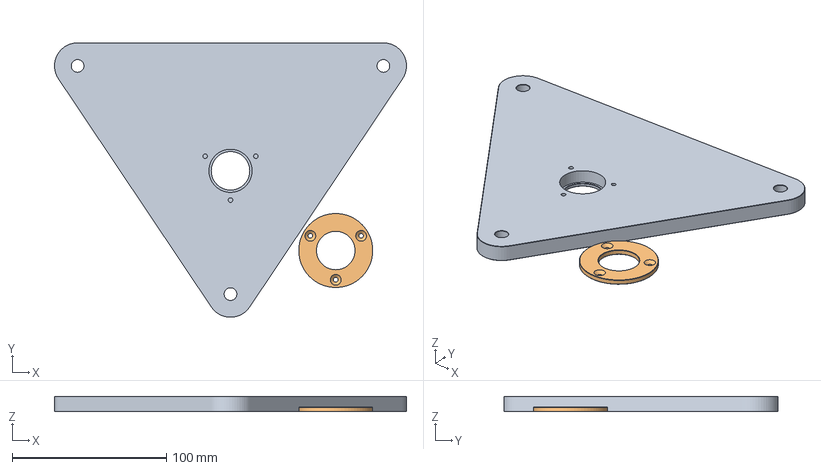
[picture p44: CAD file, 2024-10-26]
3MF/Outer Plate PLA GREEN.3mf
228.4 x 178.0 x 10.0 mm

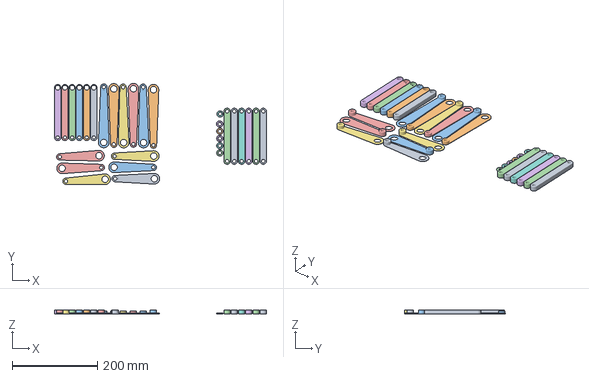
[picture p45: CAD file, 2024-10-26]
3MF/Levers PLA YELLOW.3mf
497.9 x 237.7 x 10.0 mm

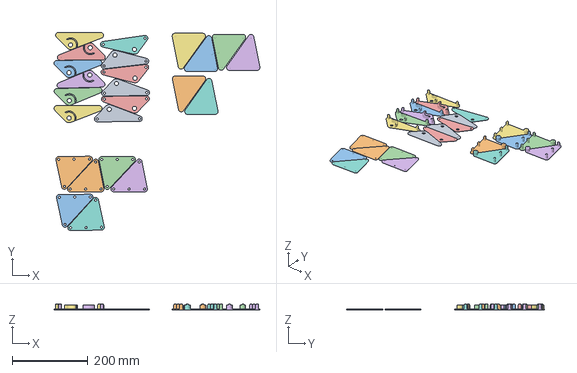
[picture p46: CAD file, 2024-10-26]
3MF/Leg Plates PLA RED.3mf
545.3 x 524.5 x 16.4 mm

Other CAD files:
STP/Frame and Crank v11.step
STP/old/Frame and Crank v11.step
3MF/M8 Cylinder v1.3mf

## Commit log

2024-10-31 added images, reshuffled the files
    [Cranks v19.step, Frame and Crank v11.step, Gearbox Frame v20.step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]
2024-10-31 + feet and spacers
    [Feet v34.3mf, Spacers PLA BLACK.3mf]
